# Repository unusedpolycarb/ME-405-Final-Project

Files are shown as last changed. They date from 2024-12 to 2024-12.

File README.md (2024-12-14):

# Romi-O (was not built in a day)



## Romi-O's Time Trial (click to watch!)

Watch our trial here! (https://youtu.be/ucUNd86v_RI?si=cy1BHj5UCIDBjYc2)

## Mechanical Design
The Romi robot consists of a plastic base, bought from Pololu, upon which two DC motors are mounted. A laser-cut acrylic piece is attached to the base via multiple metal stand offs (provided by our professor). The Nucleo L476 sits atop this acrylic piece.  


A 3d printed fixture was designed to attach the IR sensor array and two limit switches to the front of the Romi. A CAD model approximation of the IR array and the CAD model of the mount are provided in SolidWorks format.

## Electrical Design

### The overall electrical layout:


### BNO055 IMU Sensor  


Purpose: Measures yaw, pitch, and roll for navigation. Used for rotational feedback and precise movement adjustments. 
 
### Infrared (IR) Sensors (ITR2001)   



Purpose: Line-following detection. Implemented within an array of five sensors for calculating the total line deviation by using weights. 
Thresholds: Includes ceiling and floor thresholds for signal normalization. Each sensor was experimentally tested until each of the thresholds were found.  
 
### Bump Sensors (KW12)  



Purpose: Detect collisions with objects.

The Romi's interaction with the sensor data is facilitated by the STM32L476 Microcontroller. The array of infared sensors allow the robot to calculate a total deviation away from the line. This was done by attaching weights to each infared sensor, and the analog values were read in from the ADC. A BNO055 inertial measurement unit (IMU) is utilized for orientation tracking, providing yaw, pitch, and roll data critical for maintaining stability and accurate directional acceleration control. Additionally, two KW12 bump sensors are mounted on the front corners of the robot to detect collisions with obstacles, ensuring safety and triggering corrective maneuvers. The sensors receive power from the Nucleo board itself while the motors receive power from the Romi's Power Distrubution Board. The robot's mobility is powered by two DC motors, each controlled by an L6206 motor driver for speed and direction control. Each motor is paired with an encoder to provide feedback on wheel speed, essential for closed-loop control and precise velocity adjustments. The motors drive the wheels via PWM signals, with encoders measuring rotational speed to maintain consistent motion. Further documentation of each of the sensors can be found in Documentation/Electrical.

## Software Design
The program is structured around a cooperative task-based architecture. There are three tasks: the controller task, motor task, and user input task. Tasks share information with each other through a share (a positive integer) and a queue of positive integers. Each task has multiple states that it cycles through.

The limitations on what information each task can share were very difficult to work with. The solution our team came up with was to create flags, which would be placed in the “share” variable, and put additional relevant information for that flag in the queue. Below is a list of possible flags and the required information:
 


### Controller Task:
The controller task is specifically tuned to each challenge. In this case, it is specifically tuned to every step in the maze. As such, there are 22 states which progress in sequence. Each state will only exit upon a certain condition being completed. For example, the program will only exit the line following state (2) if the it senses the bump sensors were pressed. The full sequence is shown below:



### Motor Task:
The motor task keeps track of two state variables, one for the right motor and one for the left motor. For each motor, three states are possible. The first corresponds to static controls which only have to be called once. Commands such as set_motor_duty and set_motor_speed fall into this category because only one call to the motor driver is needed. State 2 refers to our trapezoidal velocity profile state. In this state multiple calls to the motor driver are made, as the motor velocity ramps toward the target velocity. State 3 implements our PI control for the Romi yaw rate, setting corrected motor speeds each time it polls the IMU.



### User Input Task:
The user input task is very simple with only two states for every possible button (of which there are three). Upon noticing that the button has been pressed, it will move to state 2 where it attempts to raise the appropriate flag repeatedly. If it successfully raises the corresponding flag, it will return to state 1 and continue polling for button presses.



## Control System
Our basic control system relies on reading the line deviation and converting that into a yaw acceleration to correct for the deviation. Over time that acceleration compiles and changes the yaw rate. 
In other systems made by our classmates, when the deviation was zero the yaw rate was set to zero. This means that their robot will periodically under-turn when following a line of constant curvature. The benefit of our design is that when the deviation is zero, the acceleration is zero and the yaw rate is constant. This allows it to follow lines of constant curvature without periodically under or overturning.

However, our system has multiple issues in practice. The first one being because yaw_accel can only gradually change target_yaw_rate over time, the system is typically slow to correct and loses the line during tight turns. To fix this we added extra logic to this controller.

`if deviation > 16:
      yaw_rate = MAX_YAW_MAX_DEV`
      
`if deviation < -16:
      yaw_rate = -MAX_YAW_MAX_DEV`

This bypasses the acceleration when the deviation is above a certain threshold, allowing the Romi to quickly adjust itself back onto the line. In the future, instead of using a linear function to convert line_deviation into yaw_acceleration, we recommend using a cubic polynomial which will naturally evaluate large accelerations at extreme deviations.

### PID Velocity Control



We use a PID loop with feed forward control to accurately set the velocity of each motor. The block diagram is shown above. 
We also implemented yaw rate control, using feedback from the BNO055 gyroscope. This system wraps around the PID velocity control and only uses P and I elements. This is shown in the block diagram below. 



Altogether this system allows us to set the forward velocity and yaw rate of the Romi. This capability is most clearly used during the “box maneuver” where the Romi traces a semicircle around the box obstacle. It is also a key part of our line following algorithm, since our line following control outputs a yaw_rate.

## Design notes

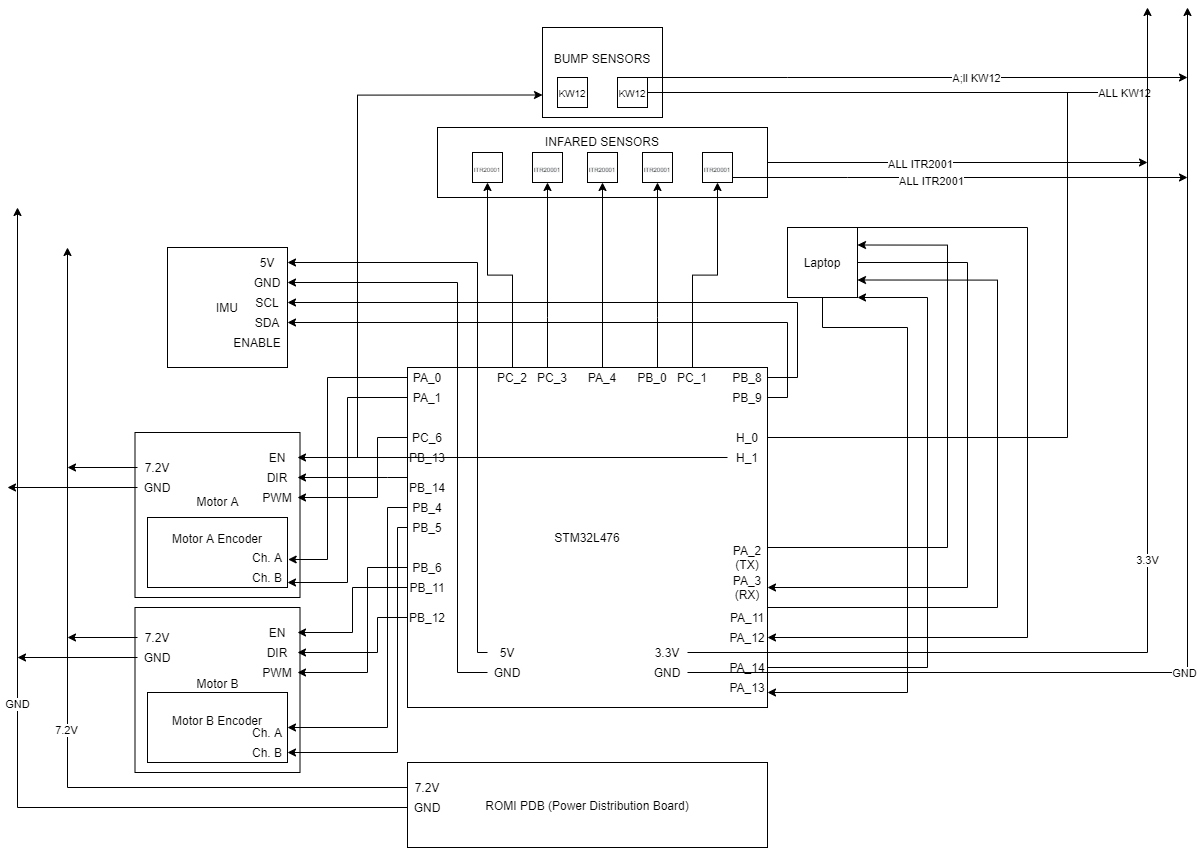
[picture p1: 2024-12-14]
Documentation/Electrical/Overall Electrical Diagram.png

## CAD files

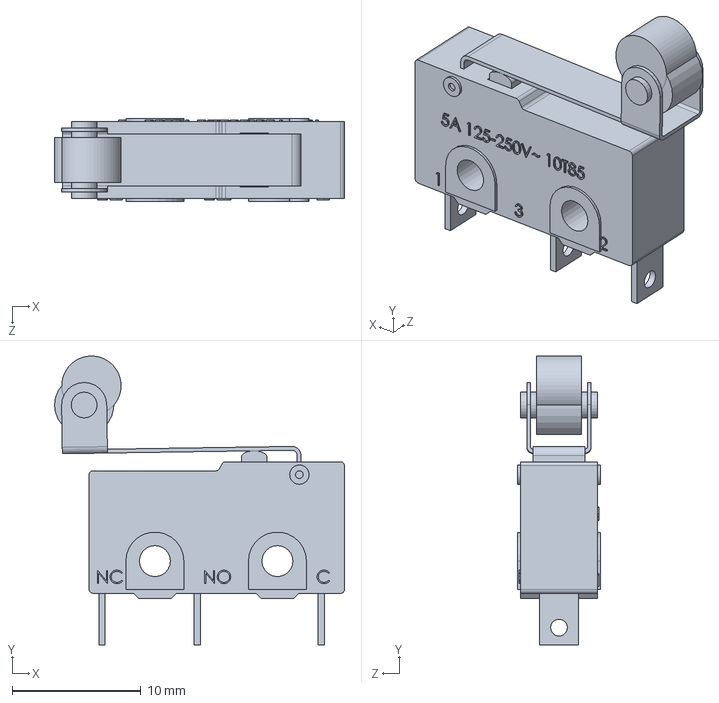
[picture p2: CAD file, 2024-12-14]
CAD/microswitch 10T85.SLDPRT
22.5 x 22.4 x 6.40 mm

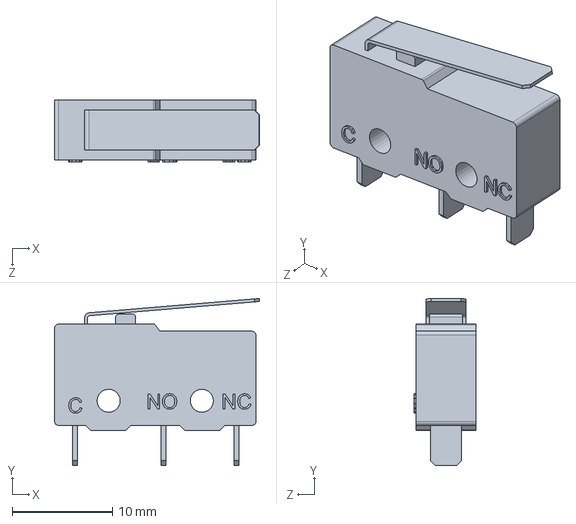
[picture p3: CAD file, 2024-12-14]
CAD/Fim de curso v3.SLDPRT
20.4 x 16.7 x 6.20 mm

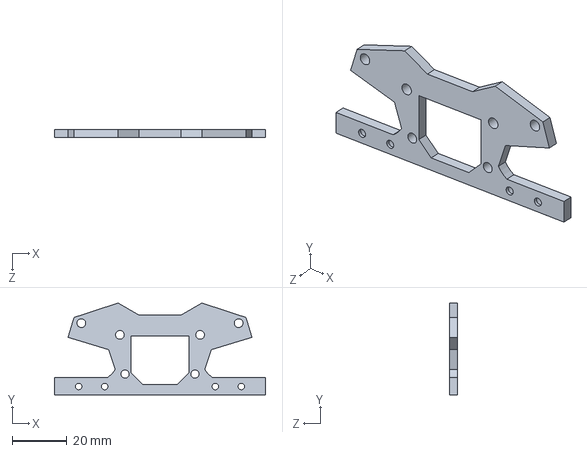
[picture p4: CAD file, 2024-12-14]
CAD/Part24.SLDPRT
77.0 x 33.5 x 3.05 mm

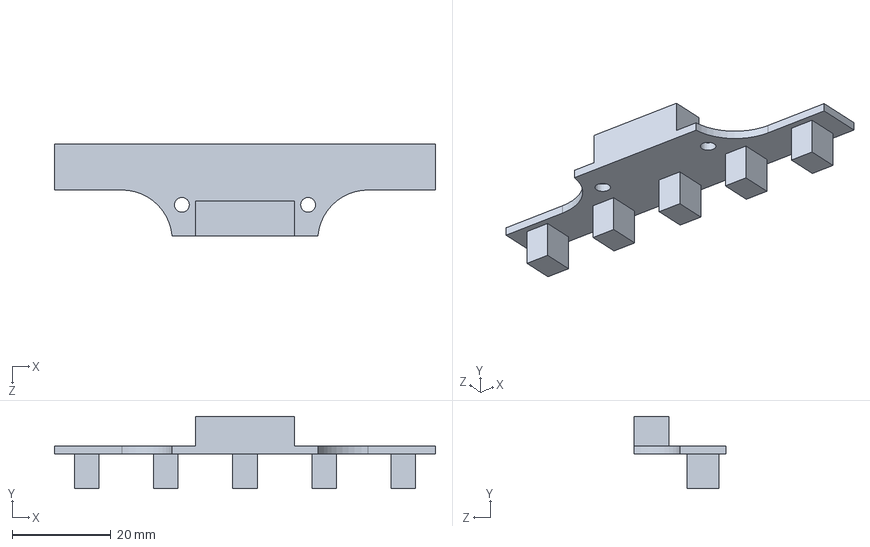
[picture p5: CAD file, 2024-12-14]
CAD/Part23.SLDPRT
77.0 x 14.6 x 18.5 mm

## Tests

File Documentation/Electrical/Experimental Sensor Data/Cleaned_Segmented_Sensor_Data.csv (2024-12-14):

Index | Region | time | Sensor_1 | Sensor_2 | Sensor_3 | Sensor_4 | Sensor_5
3 | White | 3 | 3846 | 3839 | 3855 | 3853 | 3834
4 | White | 4 | 3875 | 3867 | 3879 | 3875 | 3857
5 | White | 5 | 3866 | 3859 | 3871 | 3867 | 3848
6 | White | 6 | 3865 | 3858 | 3871 | 3867 | 3848
7 | White | 7 | 3858 | 3851 | 3865 | 3861 | 3841
8 | White | 8 | 3859 | 3852 | 3866 | 3860 | 3841
9 | White | 9 | 3858 | 3853 | 3867 | 3861 | 3841
10 | White | 10 | 3857 | 3852 | 3866 | 3860 | 3839
11 | White | 11 | 3859 | 3854 | 3867 | 3861 | 3841
12 | White | 12 | 3859 | 3854 | 3867 | 3861 | 3841
13 | White | 13 | 3859 | 3855 | 3865 | 3863 | 3842
14 | White | 14 | 3859 | 3848 | 3865 | 3861 | 3841
15 | White | 15 | 3859 | 3846 | 3866 | 3860 | 3842
16 | White | 16 | 3859 | 3852 | 3867 | 3859 | 3843
17 | White | 17 | 3858 | 3851 | 3866 | 3859 | 3839
18 | White | 18 | 3859 | 3851 | 3866 | 3860 | 3839
19 | White | 19 | 3858 | 3858 | 3867 | 3861 | 3841
20 | White | 20 | 3856 | 3854 | 3868 | 3859 | 3842
21 | White | 21 | 3859 | 3853 | 3867 | 3861 | 3843
22 | White | 22 | 3859 | 3855 | 3867 | 3860 | 3841
23 | White | 23 | 3859 | 3855 | 3867 | 3863 | 3839
24 | White | 24 | 3859 | 3853 | 3867 | 3861 | 3842
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

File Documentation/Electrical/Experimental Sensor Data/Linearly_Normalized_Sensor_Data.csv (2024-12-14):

Intensity | Sensor_1 | Sensor_2 | Sensor_3 | Sensor_4 | Sensor_5
1.0 | 0.9818128483426225 | 0.983981014535746 | 0.9834954317712938 | 0.9834661942722173 | 0.9793996468510888
1.0 | 0.9882663537694338 | 0.9899139721150993 | 0.9879162982611258 | 0.988780631827576 | 0.9864626250735727
1.0 | 0.9988266353769434 | 0.9994067042420647 | 0.9982316534040672 | 0.9994095069382934 | 0.9994114184814596
1.0 | 0.9991199765327076 | 0.999110056363097 | 0.9982316534040672 | 0.9985237673457337 | 0.9979399646851089
1.0 | 0.9976532707538868 | 0.9994067042420647 | 0.9985263778367227 | 0.998819013876587 | 0.9988228369629194
1.0 | 1.0 | 1.0 | 1.0 | 1.0 | 1.0
1.0 | 0.9973599295981226 | 0.9976268169682587 | 0.9967580312407899 | 0.9970475346914673 | 0.9970570924072985
1.0 | 0.9909064241713113 | 0.99110056363097 | 0.9905688181550251 | 0.9911426040744021 | 0.9905826957033549
1.0 | 0.9903197418597829 | 0.99110056363097 | 0.9902740937223696 | 0.9908473575435489 | 0.9905826957033549
1.0 | 0.9900264007040188 | 0.9905072678730347 | 0.9905688181550251 | 0.9908473575435489 | 0.9911712772218952
1.0 | 0.9903197418597829 | 0.99110056363097 | 0.9905688181550251 | 0.9905521110126956 | 0.9899941141848146
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

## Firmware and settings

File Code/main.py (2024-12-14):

#notes about lab structure:


#Use the cotask class to create a list of tasks (which are generator methods) that run cooperatively
#Each generator method must take in a tuple of (share, queue)
#Each generator method must yield the next state number for that task, this history stored in Task.trace
#Because it is a generator method, the state variable continues to exist within that task between function calls
#Both share and queue function as queues. Idk how they're different



#import statements
from pyb import Pin, Timer, I2C, UART
from src.BNO055_communication import BNO055
from src.romi_flags import RomiFlags
from src.IR_array import IR_array, IR_sensor
import utime
import struct
#import keyboard
from src.motor3 import L6206
from src import cotask, task_share
#credit to https://github.com/spluttflob/ME405-Support/blob/main/examples/basic_tasks.py for code in this lab
import gc


#how many different time loops are in our code currently?
# motor PWM
# encoder update
# checking for button press (user input)
# data collection



#setup method: runs once at beginning of program
def setup():
    pass
    #not sure if we should do all the definitions here, or in state 0 of task 2?
    #create motor objects
    #create encoder objects
    #enable everything, but don't run the motors


def bandpass(values, floor_thresholds, ceil_thresholds):
    for i in range(len(values)):
        values[i] = 1 - (floor_thresholds[i] - values[i]) / (floor_thresholds[i] - ceil_thresholds[i])
        if values[i] < 0:
            values[i] = 0
        if values[i] > 1:
            values[i] = 1
    return values


def normalize_list(values):
    min_val = min(values)
    max_val = max(values)

    if max_val - min_val == 0:
        return [0 for _ in values]
    
    total = sum(values)
    
    return [val/total for val in values]


def task1(shares):
    '''@brief: controller task'''
    
    ceil_thresholds = [3840, 3830, 3850, 3840, 3830]
    floor_thresholds = [2800, 3200, 2955, 3300, 2900]
    weights = [-22, -11, 0, 11, 22]

    DEAD_ZONE = 6
    MAX_DEV = 22
    V_TAN = 7.2 #rad/s
    delta_T = 0.02
    MAX_STEP = 1 #rad/s^2  
    MAX_YAW = 0.8
    MAX_YAW_MAX_DEV = 2.1


    IR_1 = IR_sensor(Pin.cpu.C2,3840)
    IR_2 = IR_sensor(Pin.cpu.C3,3830)
    IR_3 = IR_sensor(Pin.cpu.A4,3850)
    IR_4 = IR_sensor(Pin.cpu.B0,3840)
    IR_5 = IR_sensor(Pin.cpu.C1,3830)

    my_array = IR_array([IR_1, IR_2, IR_3, IR_4, IR_5])

    TRACK_WIDTH = 5.5 #in 
    CORRECTIVE_YAW = 2 #rad/s
    WHEEL_RADIUS = 1.375 #in
    CORRECTIVE_VEL = CORRECTIVE_YAW*TRACK_WIDTH/2/WHEEL_RADIUS #rad/s, evaluates to 4 rad/s
    
    NOMINAL_WHEEL_VEL = 20 #rad/s


    max_accel = 8 #rad/s^2
    state = 1

    mot_A_vel = NOMINAL_WHEEL_VEL #rad/s
    mot_B_vel = NOMINAL_WHEEL_VEL #rad/s
    yaw_rate = 0
  
    counter = 0
    counter_two = 0

    yield state
    while True:
        my_share, my_queue = shares
        flag = my_share.get()

        line_results = my_array.get_vals()
        deviation = 0
        line_results = bandpass(line_results, floor_thresholds, ceil_thresholds)
        line_results = normalize_list(line_results)

        for i in range(len(line_results)):
            deviation += line_results[i] * weights[i]

        if state == 1 and flag == RomiFlags.nucleo_button_press:
            print("yaw capture flag")
            my_share.put(RomiFlags.initial_yaw_capture)
            flag = None
            #state = 20
            state = 20

        if state == 20 and flag == RomiFlags.none:
            #start both motors at a reasonable speed
            print("A")
            my_share.put(RomiFlags.trap_velocity)
            my_queue.put(2)
            my_queue.put(int(mot_A_vel*1000*0.5))
            my_queue.put(1)
            my_queue.put(int(max_accel*1000))
            my_queue.put(int(mot_B_vel*1000*0.5))
            my_queue.put(1)
            my_queue.put(int(max_accel*1000))
            yaw_rate = 0
            state = 2
        
        

        if state == 2:
            #print(deviation)

            if abs(deviation) < DEAD_ZONE:
                step = 0
            
            elif counter > 0:
                counter = 0
                step = MAX_STEP * 20 * deviation / MAX_DEV * delta_T 
                yaw_rate += step

                #saturate yaw rate 
                if yaw_rate > MAX_YAW:
                    yaw_rate = MAX_YAW
                if yaw_rate < -1 * MAX_YAW:
                    yaw_rate = -1 * MAX_YAW

                #print(f"rate: {yaw_rate}, step: {step} dev: {deviation}")

                if deviation > 16:
                    yaw_rate = MAX_YAW_MAX_DEV
                
                if deviation < -16:
                    yaw_rate = -MAX_YAW_MAX_DEV
                   
                
                
                my_share.put(RomiFlags.yaw_and_speed)
                my_queue.put(abs(int(V_TAN*1000)))
                my_queue.put(1)
                my_queue.put(int(8*1000))
                my_queue.put(int(abs(yaw_rate)*1000))
                
                if yaw_rate < 0:
                    my_queue.put(0)
                else:
                    my_queue.put(1)

            else:
                counter += 1

        #if button flag raised     
        if flag == RomiFlags.switch_A or flag == RomiFlags.switch_B:
            print("wall hit")
            my_share.put(RomiFlags.soft_disable_motor)
            my_queue.put(2)
            counter = 0
            state = 3
            #stop both motors
            #proceed to state 3

        #just a wait state
        if state == 3:
            counter += 1
            if counter > 10:
                state = 4

        if state == 4 and flag == RomiFlags.none:
            print("backing up")
            my_share.put(RomiFlags.trap_velocity)
            my_queue.clear()
            my_queue.put(2)
            my_queue.put(int(2*1000))
            my_queue.put(0)
            my_queue.put(int(max_accel*1000))
            my_queue.put(int(2*1000))
            my_queue.put(0)
            my_queue.put(int(max_accel*1000))
            counter = 0
            state = 5
        
        if state == 5:
            counter += 1
            if counter > 50:
                state = 6

        if state == 6:
            my_share.put(RomiFlags.soft_disable_motor)
            flag = None
            my_queue.put(2)
            state = 7

        if state == 7 and flag == RomiFlags.none:
            my_share.put(RomiFlags.turn_90)
            my_queue.put(1)
            state = 8
            print("turning 90")
            #turn 90 degrees

        if state == 8 and flag == RomiFlags.soft_disable_motor:
            print("recognized arrival")
            state = 9

        if state == 9 and flag == RomiFlags.none:
            #set an alarm
            print("set the yaw alarm")
            my_share.put(RomiFlags.yaw_alarm)
            flag = None
            my_queue.clear()
            my_queue.put(150)
            my_queue.put(0)
            state = 10

        
        if state == 10 and flag == RomiFlags.none:
            
            TURN_RADIUS = 13.7 #in
            WHEEL_VEL = 14 #rad/s
            TANGENTIAL_VEL = WHEEL_VEL*WHEEL_RADIUS

            TRACK_WIDTH = 5.5 #in   
            WHEEL_RADIUS = 1.375 #in

            YAW_RATE = TANGENTIAL_VEL/TURN_RADIUS

            my_share.put(RomiFlags.yaw_and_speed)
            my_queue.clear()
            my_queue.put(int(WHEEL_VEL*1000))
            my_queue.put(1)
            my_queue.put(int(8*1000))
            my_queue.put(abs(int(YAW_RATE*1000)))
            my_queue.put(0)
            flag = None
            state = 11

        if state == 11:
            if flag == RomiFlags.yaw_alarm_return:
                print("target heading reached")
                my_share.put(RomiFlags.soft_disable_motor)
                my_queue.put(2)
                state = 12
        
        if state == 12 and flag == RomiFlags.none:
            print("reached here")
            my_share.put(RomiFlags.trap_velocity)
            my_queue.put(2)
            my_queue.put(int(mot_A_vel*1000))
            my_queue.put(1)
            my_queue.put(int(max_accel*1000))
            my_queue.put(int(mot_B_vel*1000))
            my_queue.put(1)
            my_queue.put(int(max_accel*1000))
            yaw_rate = 0
            counter_two = 0
            state = 13
        
        if state == 13:
            #print("line follow again")
            if abs(deviation) < DEAD_ZONE:
                step = 0
            
            elif counter > 0:
                counter = 0
                step = MAX_STEP * 20 * deviation / MAX_DEV * delta_T 
                yaw_rate += step

                #saturate yaw rate 
                if yaw_rate > MAX_YAW:
                    yaw_rate = MAX_YAW
                if yaw_rate < -1 * MAX_YAW:
                    yaw_rate = -1 * MAX_YAW

                #print(f"dev: {deviation}")

                if deviation > 16:
                    yaw_rate = MAX_YAW_MAX_DEV
                
                if deviation < -16:
                    yaw_rate = -MAX_YAW_MAX_DEV
                   
                
                
                my_share.put(RomiFlags.yaw_and_speed)
                my_queue.clear()
                my_queue.put(abs(int(V_TAN*1000)))
                my_queue.put(1)
                my_queue.put(int(8*1000))
                my_queue.put(int(abs(yaw_rate)*1000))
                
                if yaw_rate < 0:
                    my_queue.put(0)
                else:
                    my_queue.put(1)

            else:
                counter += 1
            
            counter_two += 1
            if counter_two > 120:
                number_of_true_sens = 0
                for val in my_array.get_line():
                    if val is True:
                        number_of_true_sens += 1
                
                if number_of_true_sens >= 4:
                    print("finish detected")
                    my_share.put(RomiFlags.yaw_and_speed)
                    my_queue.clear()
                    my_queue.put(abs(int(V_TAN*1000)))
                    my_queue.put(1)
                    my_queue.put(int(8*1000))
                    my_queue.put(int(0))
                    my_queue.put(0)
                    state = 14
                    counter = 0
       
        if state == 14:
            print("state 14")
            

            counter += 1
            if counter > 40:
                my_share.put(RomiFlags.soft_disable_motor)
                my_queue.put(2)
                state = 15
                counter = 0

        if state == 15 and flag == RomiFlags.none:
            my_share.put(RomiFlags.return_to_initial_yaw)
      
            state = 16
            print("state 15")

        if state == 16 and flag == RomiFlags.soft_disable_motor:
            print("state 16")
            state = 17
        
        if state == 17 and flag == RomiFlags.none:
            print("should be facing correctly now")
            state = 18

        if state == 18:
            # my_share.put(RomiFlags.yaw_and_speed)
            # my_queue.clear()
            # my_queue.put(abs(int(V_TAN*1000)))
            # my_queue.put(1)
            # my_queue.put(int(8*1000))
            # my_queue.put(int(0))
            # my_queue.put(0)

            my_share.put(RomiFlags.set_motor_duty)
            my_queue.clear()
            my_queue.put(2)
            my_queue.put(40)
            my_queue.put(1)
            my_queue.put(42)
            my_queue.put(1)
            state = 19
            counter = 0
            
        if state == 19:
            counter += 1
            if counter > 20:
                state = 30
            
        if state == 30:
            if False not in my_array.get_line():
                state = 31
                counter = 0

        if state == 31:
            counter += 1
            if counter > 40:
                my_share.put(RomiFlags.soft_disable_motor)
                my_queue.put(2)
                state = 32
        if state == 32 and flag == RomiFlags.none:
            state = 1

        yield state




def maxacceltest(shares):
    '''@brief: controller task'''
   
    max_accel = 2 #rad/s^2
    state = 1
    print("Zero")
    yield state
    while True:
        my_share, my_queue = shares
        flag = my_share.get()
        if state == 1 and flag == RomiFlags.nucleo_button_press:
            print("A")
            my_share.put(RomiFlags.trap_velocity)
            flag = None
            my_queue.put(2)
            my_queue.put(int(15*1000))
            my_queue.put(1)
            my_queue.put(int(max_accel*1000))
            my_queue.put(int(15*1000))
            my_queue.put(1)
            my_queue.put(int(max_accel*1000))
            state = 2

        if state == 2 and flag == RomiFlags.nucleo_button_press:
            print("C")
            #soft disable both motors
            my_share.put(RomiFlags.soft_disable_motor)
            my_queue.put(2)
            state = 3

        if state == 3 and flag == RomiFlags.none:
            #calculate new max accel
            max_accel += 2
            print(f"new max accel: {max_accel}")
            state = 1

        yield state

def task1deprecated(shares):
    '''@brief: controller task'''
    my_share, my_queue = shares

    #Calculate mot_A and mot_B speeds
    tangential_speed = 2 #in/s
    radius = 12 #in
    WHEELBASE = 2.75 #in
    WHEEL_RADIUS = 1.375 #in
    THRESHOLD = 100 #EULER YAW (ticks)
    SEMICIRCLE_ANGLE = 2880 #(ticks)

    chirality = "CCW"
    v_A = tangential_speed/radius*(radius+WHEELBASE)/WHEEL_RADIUS
    v_B = tangential_speed/radius*(radius-WHEELBASE)/WHEEL_RADIUS


    if chirality == "CW":
        v_A, v_B = v_B, v_A

    i2c = I2C(1, I2C.CONTROLLER, baudrate=100000)
    utime.sleep_ms(100)
    imu = BNO055(i2c)

    initial_eul_yaw = 0
    print("Done with Initial Calibration and Setup")
    imu.change_mode("IMU")
    completed_half_circle = False

    state = 1
    yield state

    while True:
        flag = my_share.get()

        #if button is pressed and unpressed, get current Euler and set speed for both motors
        if state == 1:
            #print(imu.get_cal_status())
            #polls the EULER HEADING, or yaw, everytime that the system enters this part of the loop
            #print(f"EUL yaw: {EUL_yaw}")
            pass

        #in this state, the system will wait for the nucleo button to be pressed before it sets Motor A on
        if state == 1 and flag == RomiFlags.nucleo_button_press:
            #takes initial EULER YAW measurement to compare with future values for stopping the system
            initial_eul_yaw = imu.get_EUL_heading()
            my_share.put(RomiFlags.set_motor_speed)
            my_queue.put(0)
            my_queue.put(int(v_A*1000))
            my_queue.put(1)
            state = 2
            #automatic transition to set Motor B on as well

        #happens seamlessly
        if state == 2 and flag == RomiFlags.none:
            my_share.put(RomiFlags.set_motor_speed)
            my_queue.put(1)
            my_queue.put(int(v_B*1000))
            my_queue.put(1)
            state = 3


        #this state keeps track of Romi's progress around the circle
        if state == 3:
            #check for semicircle travel
            eul_yaw = imu.get_EUL_heading()
            
            diff_yaw = eul_yaw - initial_eul_yaw

            if (diff_yaw > SEMICIRCLE_ANGLE):
                diff_yaw -= SEMICIRCLE_ANGLE*2
            elif (diff_yaw < -1 * SEMICIRCLE_ANGLE):
                diff_yaw += SEMICIRCLE_ANGLE*2

            withinThreshold = abs(diff_yaw) < THRESHOLD
            print(f"EUL: {eul_yaw}, init: {initial_eul_yaw}, diff: {diff_yaw}, semi:{completed_half_circle}, within: {withinThreshold}")
            if abs(diff_yaw) >= 400:
                completed_half_circle = True

            if completed_half_circle and withinThreshold:
                print("AROUND THE WORLD")
                state = 4

        #in the case that the motors were indeed turned on, the motors now need to be turned off because
        #the ROMI has now reached the EULER Yaw of 0, which indicates a full rotation around the circle.
        if state == 4 and flag == RomiFlags.none:
            print("stop A")
            my_share.put(RomiFlags.disable_motor)
            my_queue.put(2)
            state = 5
        
        if state == 5 and flag == RomiFlags.none:
            completed_half_circle = False
            state = 1

        yield state

#task 2: motor pwm setting, encoder updates, and CL control calculations
def task2(shares):
    '''@brief: task for motor pwm setting, encoder updates, and CL control calculations'''
    state = 0
    my_share, my_queue = shares
    
#Motor A
    #Left Side Encoder
       #PA0 Tim5.1, 
       #PA1 Tim5.2 

    #Left Side Motor
       #PC6 Tim3.1
       #PB13  Enable
       #PB14  Direction
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

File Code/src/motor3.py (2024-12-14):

'''!@file encoder.py
@brief A driver for reading from Quadrature Encoders
@details
@author Ritvik Dutta, Vincent Ngo
@date October 10, 2024
'''
from pyb import Pin, Timer, disable_irq, enable_irq
import utime


class L6206:
    '''DC Motor driver, uses PWM, you can set the duty cycle and speed'''

    K_V = 4 #rad/s-V
    SUPPLY_VOLTAGE = 7.2 #Volts
    MAX_VEL = SUPPLY_VOLTAGE*K_V

    #K_ff = 0
    #K_p = 0.6
    #K_i = 0.6
    #K_d = 0.1

    K_ff = 1
    K_p = 1.8
    K_i = 1.1
    K_d = 0.01
    PERIOD = 0.2 #sec

    MAX_CONTRL_EFFORT = MAX_VEL
    def __init__ (self, PWM_tim, IN1_pin, DIR_pin, EN_pin):
    #Defines global objects for rest of class to use
    #Inputs required:
    #   Timer that already has a frequency
    #   Three pins already defined

        disable_irq() #prevent silly nonsense

        self.IN1_pin = Pin(IN1_pin, mode=Pin.OUT_PP)
        self.DIR_pin = Pin(DIR_pin, mode=Pin.OUT_PP)
        self.EN_pin = Pin(EN_pin, mode=Pin.OUT_PP)
        self.EN_pin.low()  #good safety measure, ensure pin off
        self.DIR_pin.high()
        self.encoder = None
        
        #Set PID control vars
        self.PID_enable = False
        self.target_speed = 0
        self.error_was = 0
        self.error_sum = 0

        #create timer channel from timer
        self.PWM1 = PWM_tim.channel(1, mode = Timer.PWM, pin=self.IN1_pin, pulse_width_percent=0)
        self.duty = 0
        enable_irq(True)

    def set_duty (self, duty):
        '''!@brief Set the PWM duty cycle for the DC motor.
        @details This method sets the duty cycle to be sent
        to the L6206 to a given level. Positive values
        cause effort in one direction, negative values
        in the opposite direction.
        @param duty A signed number holding the duty
        cycle of the PWM signal sent to the L6206
        '''
        self.duty = duty
        #print(f"duty: {duty}")
        #if duty is positive, set DIR to one 
        if(duty >= 0 ):
            self.DIR_pin.high()
            self.PWM1.pulse_width_percent(abs(duty))
        #if duty is negative, set DIR to zero (reverses)
        else:
            self.DIR_pin.low()
            self.PWM1.pulse_width_percent(abs(duty))



    def enable(self):
        #turns the enable pin on
        self.EN_pin.value(1)

    def disable(self):
        #turns the enable pin off
        self.PID_enable = False
        self.set_duty(0)
        self.target_speed = 0
        self.EN_pin.value(0)

    def soft_disable(self):
        self.PID_enable = False
        self.set_duty(0)
        self.target_speed = 0

    class Encoder:
        '''!@brief Interface with quadrature encoders
        @details Utilizes external timers to count encoder ticks
        update() must be called at least once per timer overflow for accurate readings
        '''
        AR = 65355
        PS = 0
        TICKS_PER_REV = 1440
        PI = 3.14159

        def __init__(self, timernumber, pin1, pin2):
            '''!@brief Constructs an encoder object
            @details
            @param
            @param
            @param
            '''

            #sets timer
            self.timernumber = timernumber
            self.timer = Timer(timernumber, period = L6206.Encoder.AR, prescaler = L6206.Encoder.PS)
            #sets timer channels, which connects pins to timer
            self.timer.channel(1, pin = pin1, mode = Timer.ENC_AB)
            self.timer.channel(2, pin = pin2, mode = Timer.ENC_AB)

            #zeros the position
            self.abs_position = 0
            self.prev_position = 0
            self.cur_position = 0
            self.delta = 0
            self.speed = 0

            #vars for calculating speed
            self.time_was = utime.ticks_ms()
            self.time_is = None
            self.delta_T = None

        def update(self):
            '''!@brief Updates encoder position and delta, should be called often
            @details
            '''
            self.prev_position = self.cur_position   #moves last reading into previous position variable 
            self.cur_position = self.timer.counter()   #takes new position reading
            self.delta = self.cur_position - self.prev_position   #calculates delta between current and previous reading

            if self.delta > (L6206.Encoder.AR+1)//2:
                self.delta -= (L6206.Encoder.AR+1)

            elif self.delta < -1 * (L6206.Encoder.AR+1)//2:
                self.delta += (L6206.Encoder.AR+1)

            self.abs_position += self.delta            #

            self.time_is = utime.ticks_ms()
            self.delta_T = utime.ticks_diff(self.time_is, self.time_was)/1000 #sec
            #print(f"delta T: {self.delta_T}")
            self.time_was = utime.ticks_ms() #cant assign to time_is because object references!!

            self.speed = self.delta/self.TICKS_PER_REV*2*self.PI/self.delta_T


        def get_position(self):
            '''!@brief Gets the most recent encoder position
            '''
            return self.abs_position

        def get_delta(self):
            '''!@brief Gets the most recent encoder delta           
            '''
            return self.delta

        def get_speed(self):
            '''!@brief Gets the most recent speed data in Rad/sec'''
            return self.speed

        def get_delta_T(self):
            '''!@brief Gets the most recent delta T between readings'''
            return self.delta_T

        def zero(self):
            '''!@brief Resets the encoder position to zero
            '''
            self.abs_position = 0

    def set_encoder(self, timernumber, pin1, pin2):
        '''!@brief Creates encoder object for motor given timer and pins'''
        self.encoder = L6206.Encoder(timernumber, pin1, pin2)

    def get_encoder(self):
        '''!@brief Gets encoder object attached to this motor'''
        return self.encoder
    
    def update(self):
        '''!@brief polls encoder and updates PID effort'''
        self.encoder.update()
        #print("Checkpoint B")
        if self.PID_enable is True:
            #use utime.ticks_ms and ticks_diff to find deltaT
            current_speed = self.encoder.get_speed()
            error = self.target_speed - current_speed #rad/s
            delta_T = self.encoder.get_delta_T()

            #calc FF effort
            FF_effort = self.K_ff*self.target_speed

            #calc P effort
            P_effort = self.K_p*error

            #calc I effort
            self.error_sum += error*delta_T
            I_effort = self.error_sum*self.K_i
            
            if delta_T == 0:
                raise ValueError("delta zero boooo")

            if delta_T < 0.0001:
                raise ValueError("delta sucks")
            #calc D effort
            D_effort = self.K_d*(error - self.error_was)/delta_T
            self.error_was = error
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

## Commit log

2024-12-14 Some commits
    [Lab calculations.xlsx]
2024-12-14 Add files via upload
    Added cad files
    [Fim de curso v3.SLDPRT, Part23.SLDPRT, Part24.SLDPRT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]
2024-12-14 pushed more docs and files
    [Cleaned_Segmented_Sensor_Data.csv, Linearly_Normalized_Sensor_Data.csv, Normalized_Sensor_Data.csv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]
